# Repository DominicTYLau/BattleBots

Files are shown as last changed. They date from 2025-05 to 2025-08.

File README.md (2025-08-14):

# BattleBots

**Description:

** This project contains two battle bots that are meant to battle each other. One has a vertical spinner while the other has a horizontal one. The chassis is mostly 3D printed with some electronics for the drive base. Both bots are powered by Raspberry Pi Zero 2 W boards, each running a local server. Users connected to the same Wi-Fi network can control the bots through a web interface using arrow keys for movement and the space bar to activate the weapon.

**Motivation for this project:** I made this project because I’ve watched the larger bots and it was fun to see stuff being destroyed.

ROBOT 1: Full CAD https://a360.co/3ZUvcW5

ROBOT 2: Full CAD https://a360.co/43yXR5A

## Demo:

https://youtu.be/-OPFYqFXoV8

## Pictures:
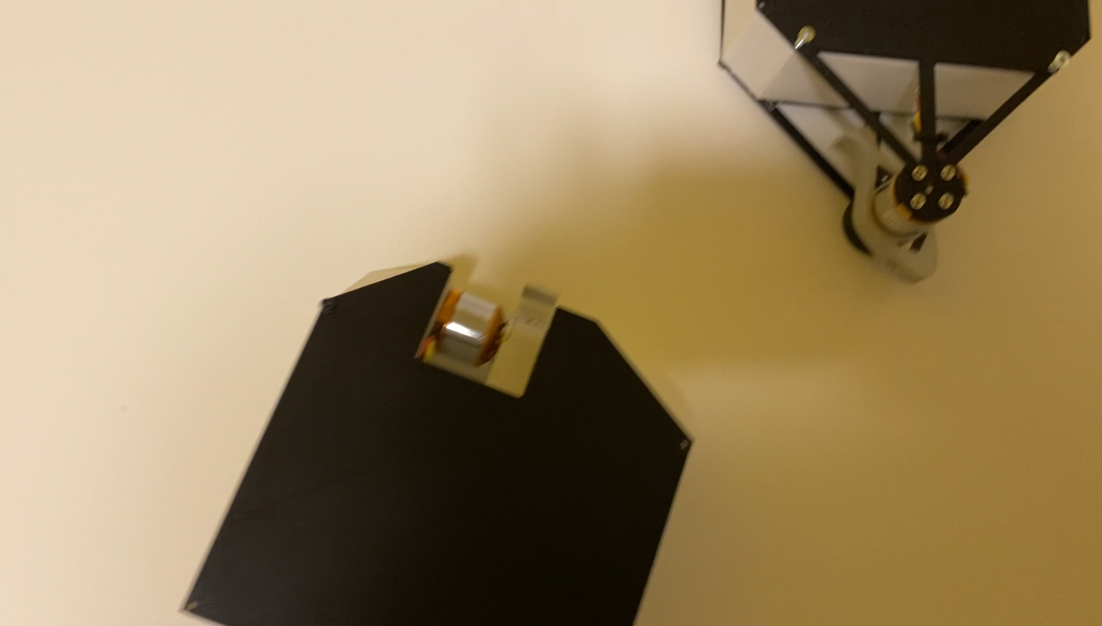
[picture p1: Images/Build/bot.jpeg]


Wiring Diagram:

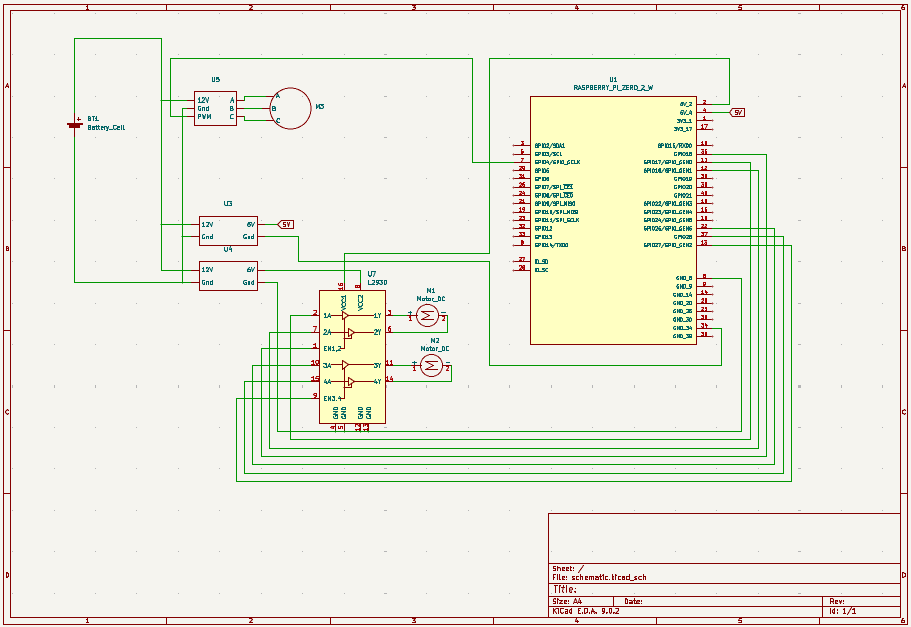
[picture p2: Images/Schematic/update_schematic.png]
High Level Schematic


## BOM:

Purchase Item:

| Item Name | What the Item Is For in Your Project | Item Source | Item Price (USD) | Quantity | Total Price (USD) | URL |
|---|---|---|---|---|---|-----|
| DC 6V Motor with gear | Used for drive motors for the robot | Amazon | 6.71 | 1 | 6.71 | [Link](https://www.aliexpress.com/item/1005005847467025.html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...) |
| CNHL 3S Lipo Battery 2200mAh 30C 11.1V (2 Packs) | Used to power Robots | Amazon | 34.72 | 1 | 34.72 | [Link](https://www.amazon.ca/CNHL-Battery-Airplane-Helicopter-Quadcopte/dp/B0B6N7BTVN/) |
| RC B3 LiPo 2S-3S Battery Charger | Used to charge lipo battery | Amazon | 12.11 | 1 | 12.11 | [Link](https://www.amazon.ca/Battery-Balancer-Charger-7-4-11-1V-Compact/dp/B06XR87987/) |
| 10pcs DC to DC Buck Converter Modules | Step down to different voltages | Amazon | 14.53 | 1 | 14.53 | [Link](https://www.amazon.ca/Podazz-Efficiency-Regulator-stabilization-Converter/dp/B0CTH5Q2KT/) |
| Wago Connectors | Connect wires, reduce mess | Amazon | 7.59 | 1 | 7.59 | [Link](https://www.amazon.ca/WAGO-221-412-Lever-Nuts-2-Conductor-Connectors/dp/B07W4RQ6R6/) |
| Terminal Connectors | Power distributions on protoboard | Aliexpress | 3.56 | 1 | 3.56 | [Link](https://www.aliexpress.com/item/1005006642865467.html) |
| Protoboard (2-8) | Power distributions | Aliexpress | 1.77 | 1 | 1.77 | [Link](https://www.aliexpress.com/item/1005006829112244.html) |
| CNC for weapon | BattleBot Weapon | JLCPCB | 83.50 | 1 | 83.50 | - |
| **Total** | | | | | **164.49** | |

Already Have

| Item | What the Item Is For in Your Project | Quantity |
|---|---|---|
| Pi Zero | Microcontroller | 2 |
| Brushless Motor | Motor | 2 |
| NRF24L01 | Transceiver | 4 |
| ESC | ESC for motor | 2 |
| Arduino Uno | Microcontroller | 2 |
| Joystick | Joystick | 4 |
| Push Button | Button | 2 |
| Bearings | For weapon system | 2 |

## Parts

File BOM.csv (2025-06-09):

Item name | What the item is for in your project | Item source | Item price (include shipping + taxes) | Quantity | Total price (USD) | URL
DC 6V Motor with gear | Used for drive motors for the robot | Amazon | 6.71 USD | 1 | 6.71 | https://www.aliexpress.com/item/1005005847467025.html?scm_id=1007.40050.354490.0&scm-url=1007.40050.354490.0
CNHL 3S Lipo Battery 2200mAh 30C 11.1V with XT60 Plug for RC Car Airplane Helicopter Quadcopte Drone,Racing Hobby(2 Packs) | Used to power Robots | Amazon | 34.72 USD | 1 | 34.72 | https://www.amazon.ca/CNHL-Battery-Airplane-Helicopter-Quadcopte/dp/B0B6N7BTVN?rnid=11192166011
RC B3 LiPo 2S-3S Battery Balancer Charger 7.4v-11.1V RC Pro Compact Charger B3AC | Used to charge lipo battery | Amazon | 12.11 USD | 1 | 12.11 | https://www.amazon.ca/Battery-Balancer-Charger-7-4-11-1V-Compact/dp/B06XR87987
10pcs DC to DC High Efficiency Voltage Regulator Step Down Module 2596 Voltage stabilization 24V to 12V 5V 3V Buck Converter | Used to step down to different voltages for each component | Amazon | 14.53 USD | 1 | 14.53 | https://www.amazon.ca/Podazz-Efficiency-Regulator-stabilization-Converter/dp/B0CTH5Q2KT
Wago Connectors | Connect wires together, decrease mess when wiring | Amazon | 7.59 USD | 1 | 7.59 | https://www.amazon.ca/WAGO-221-412-Lever-Nuts-2-Conductor-Connectors/dp/B07W4RQ6R6?rnid=11192166011
Terminal Connectors | Power distributions on protoboard | Aliexpress | 3.56 USD | 1 | 3.56 | https://www.aliexpress.com/item/1005006642865467.html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
Protoboard (2-8) | Power distributions | Aliexpress | 1.77 USD | 1 | 1.77 | https://www.aliexpress.com/item/1005006829112244.html?scm_id=1007.40050.354490.0&scm-url=1007.40050.354490.0
CNC for weapon | BattleBot Weapon | JLCPCB | 83.5 USD | 1 | 83.5
 |  |  |  |  | 164.49
Already Have
Item | What the item is for in your project | Quantity
Pi zero | Microcontroller | 2
Brushless Motor | motor | 2
NRF24L01 | Transceiver | 4
ESC | ESC for motor | 2
Arduino Uno | Microcontroller | 2
Joystick | Joystick | 4
Push Button | Button | 2
Bearings | For weapon system | 2

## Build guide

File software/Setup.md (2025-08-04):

## Prerequisites

- Raspberry Pi (with GPIO support)
- Motors + ESC connected to correct GPIO pins
- Python 3 installed
- Access to the same Wi-Fi network as your control device

## Wiring

Update the GPIO pin numbers in the script if your wiring differs.

## Setup Instructions

### 1. Connect to Raspberry Pi

### 2. Clone this repository (or copy the script)

Go to the repository

### 3. Create a virtual environment

```bash
python3 -m venv venv
source venv/bin/activate
```

### 4. Install dependencies
```bash
pip install gpiozero
```

Note: RPi.GPIO is preinstalled on most Raspberry Pi systems.

### 5. Set your Raspberry Pi’s IP address in the script

```bash
host_name = "IP_ADDRESS"
```
to your Pi’s actual local IP (e.g., "192.168.1.42")

### 6. Run the server

python3 botOne.py

If successful, you should see:

Server Starts - IP_ADDRESS

### 7. Open the controller

On a device connected to the same Wi-Fi network, open a browser and go to:

http://<raspberry-pi-ip>:8000

Controls
	•	↑ / ↓ — Forward / Backward
	•	← / → — Move left / right
	•	Spacebar — Toggle ESC-powered motor (weapon)

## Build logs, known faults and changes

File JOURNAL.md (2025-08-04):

---
title: "Battle Bot"
author: "Dominic Lau"
description: "Two Battle Bots to break each other"
created_at: "2024-06-01"
---

Time Spent: 28.5 hours

# Planning & Designing

---

## May 15, 2025

Highway was announced and it's a great time to make a project that I've always wanted. 2 BattleBots to break each other. The big challenge for this project is to make sure they both work in order to do damage.

I started by watching a lot of BattleBots and trying to find different designs from different weight classes. I then drew a couple designs that I liked.

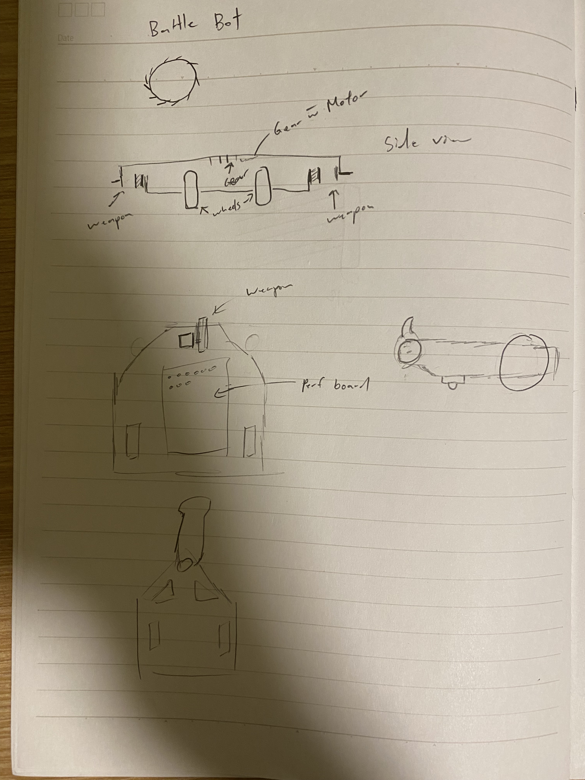
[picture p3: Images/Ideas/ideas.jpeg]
ideas


Time Spent: Around 1 hour

## May 16, 2025

Now that I had the idea, I wanted to determine how to build it. I first decided what main components I need to make this idea possible. Each robot needs to be controlled (user feedback), drive, and spin up a weapon system. Once I had an idea of the requirements, I made some high level diagrams to figure how to wire the robots. I also made a power distrubution diagram. This part is quite expensive because different components requires different voltages. In my past experiences, power is the hardest for the projects. This time, I want to wire as neatly as possible. I then broke the BOM into two main sections. Electoronics and Mechanical. After I listed everything I classified them into things I already have and things that I needed to buy. Afterwards, I went on amazon (cheapest and fastest place to get electronics for me) to find the items that I'm missing. I spent a lot of time trying to optimize the budget and keep the cost low. The current buy items are in [BOM.csv](./BOM.csv). 

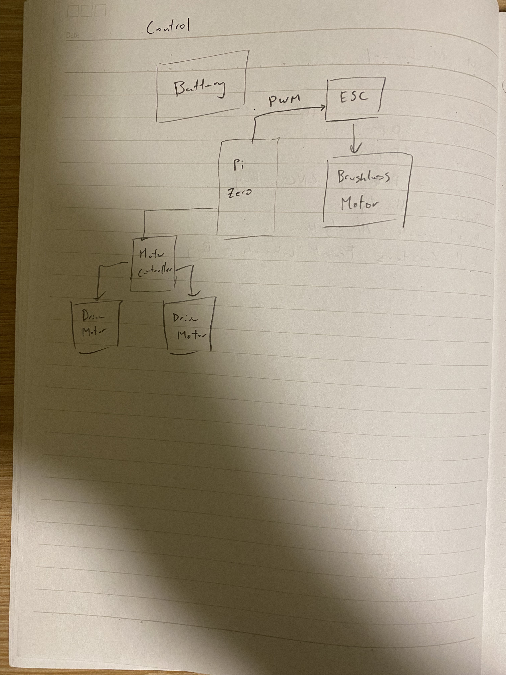
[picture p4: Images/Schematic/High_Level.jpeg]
High Level Schematic

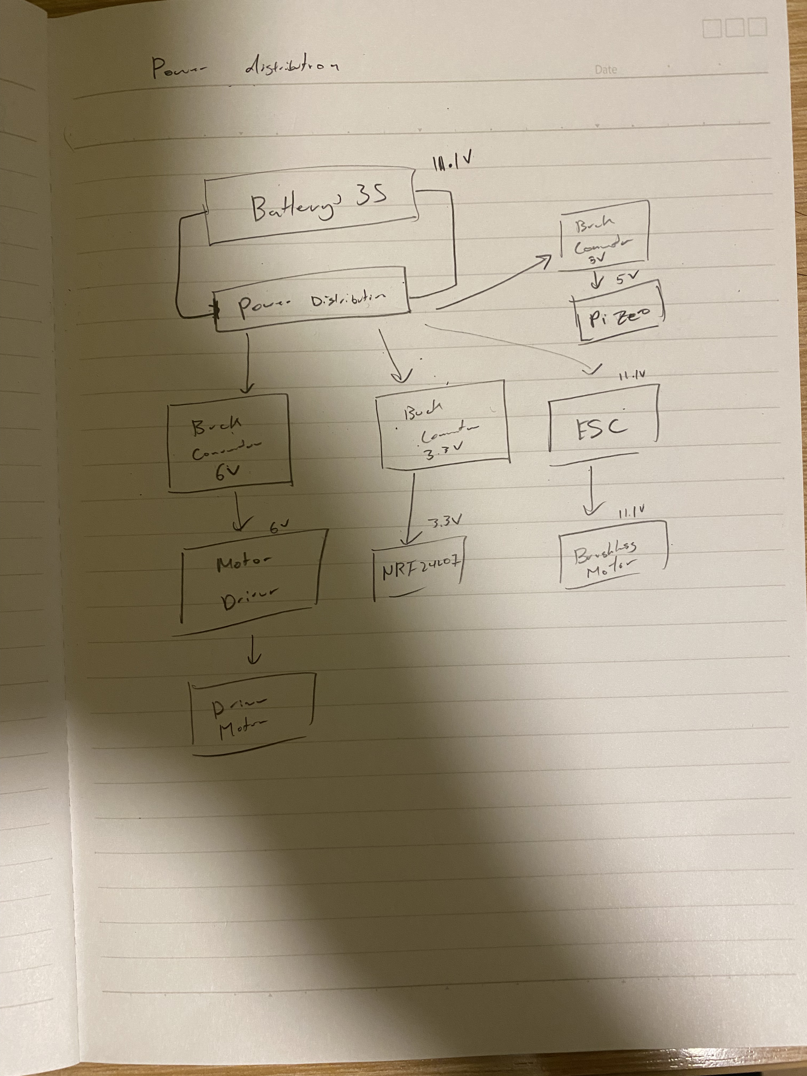
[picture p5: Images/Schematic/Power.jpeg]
Power Distribution

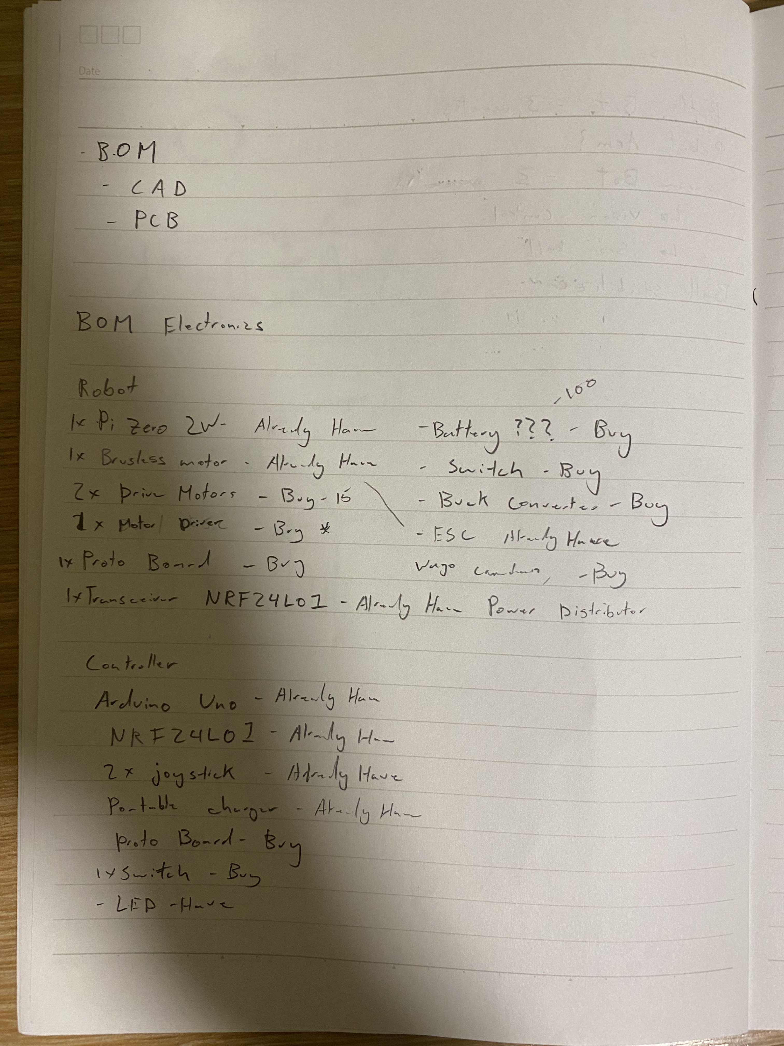
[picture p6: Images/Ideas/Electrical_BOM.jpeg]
Electrical BOM

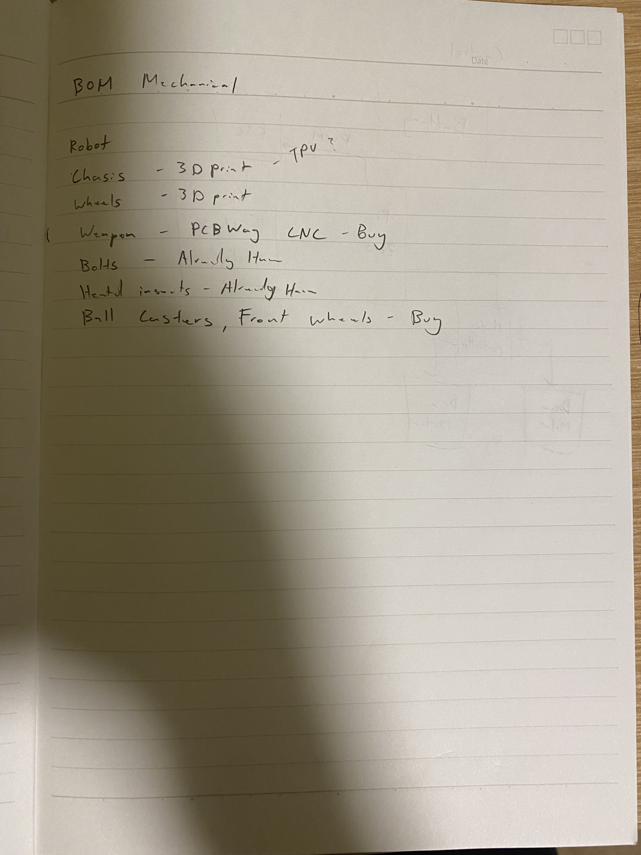
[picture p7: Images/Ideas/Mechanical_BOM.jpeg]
Mechanical BOM


Time Spent: 3 hours

## May 17, 2025

Today I spent a lot of time cading out the design. I first started by 150 mm x 150 mm square and placed each component inside where I think would best fit. After I was happy with it I moved on making it 3D. I worked on the front where I had to learn how to create planes at angles to create the angled ramps at the front of the robot. I also caded up the weapon assembly for bot 1. For bot 2, I took similar layout from bot 1 and changed where the weapon is and its support.

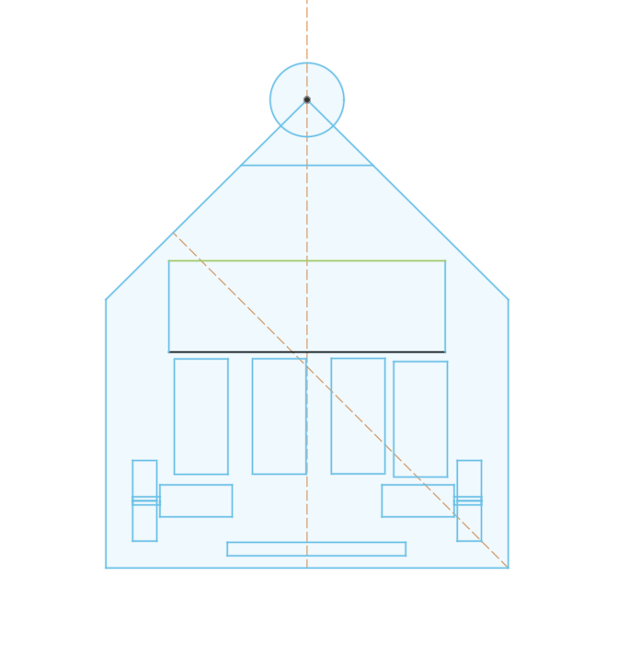
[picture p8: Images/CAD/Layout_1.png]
layout 1

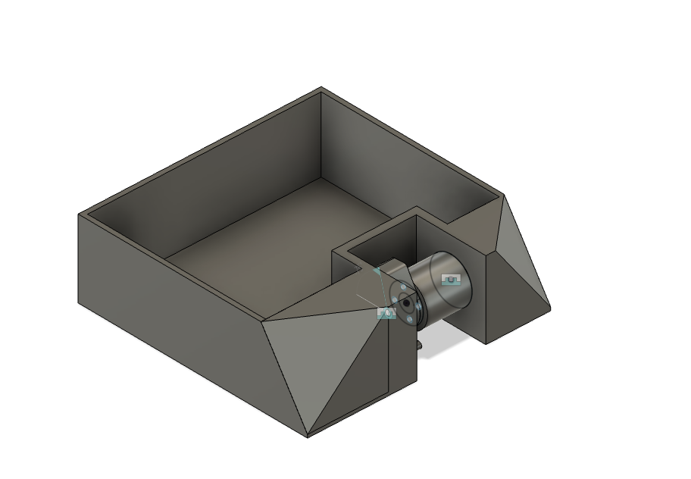
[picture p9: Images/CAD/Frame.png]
frame

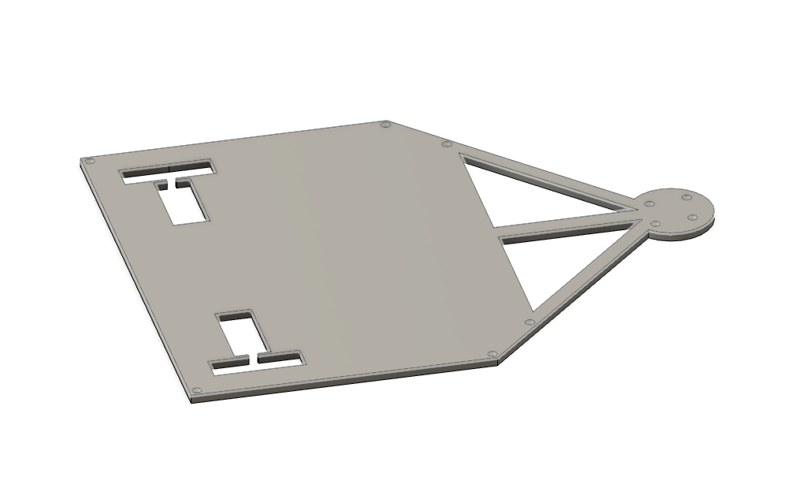
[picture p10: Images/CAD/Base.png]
base

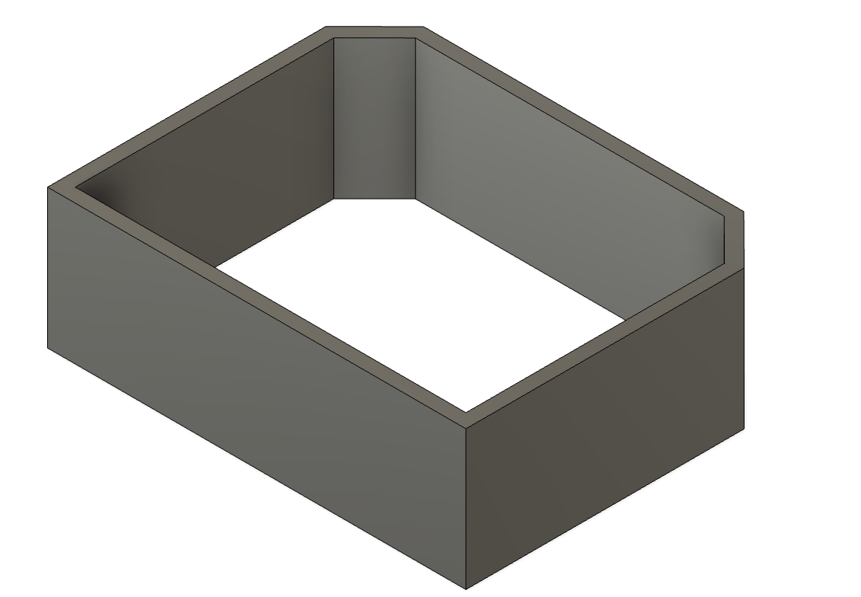
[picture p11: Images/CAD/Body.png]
body


Time Spent: 2.5 hours

## May 18, 2025

Once I had both chasis done, I decided to try and fit the components in the chassis. I followed my original layout and it worked pretty well. I also made the weapon assembly for bot 2. Most of the cad is done for bot 2. For bot 1 I added all the components but as I was adding a top I realized I made the chassis too short so I increased. However, this changed all my other values and so it looks like a mess right now. I’ll fix that for tomorrow and create a schematic.

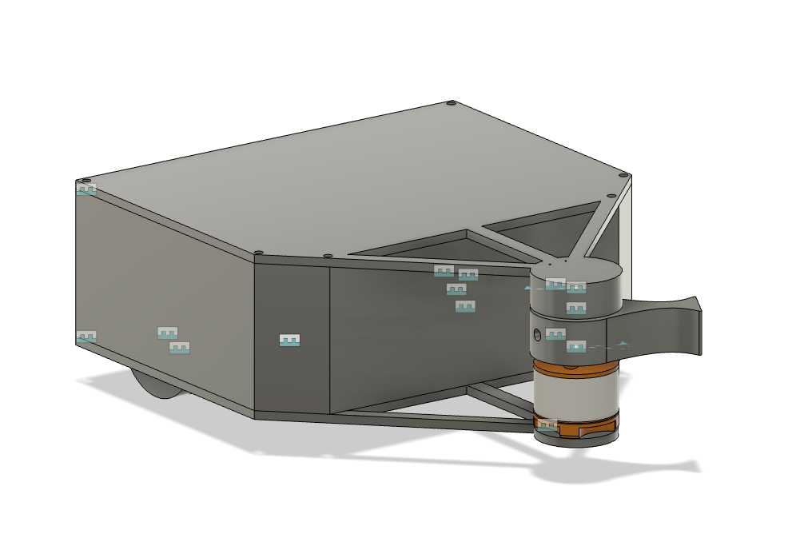
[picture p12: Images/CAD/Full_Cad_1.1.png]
cad 1.1

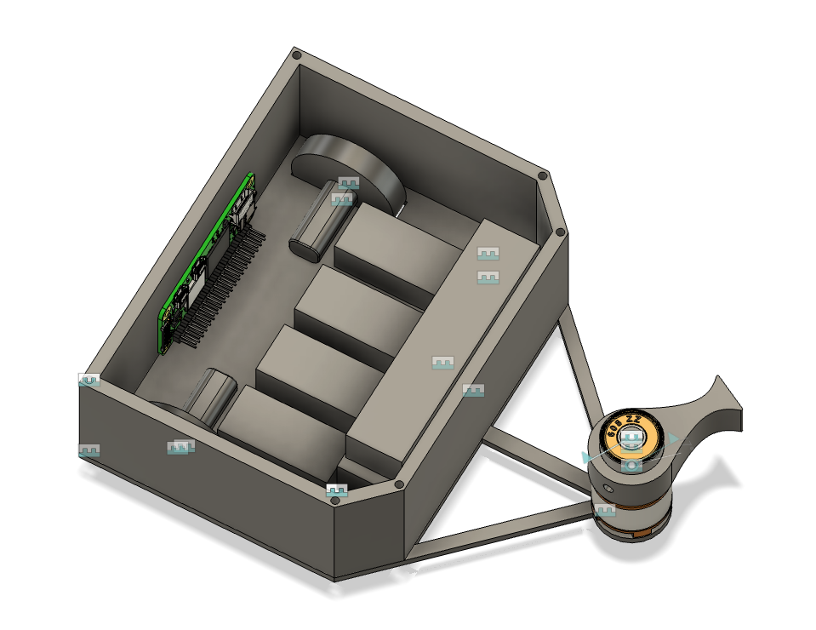
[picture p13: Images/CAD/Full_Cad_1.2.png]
cad 1.2

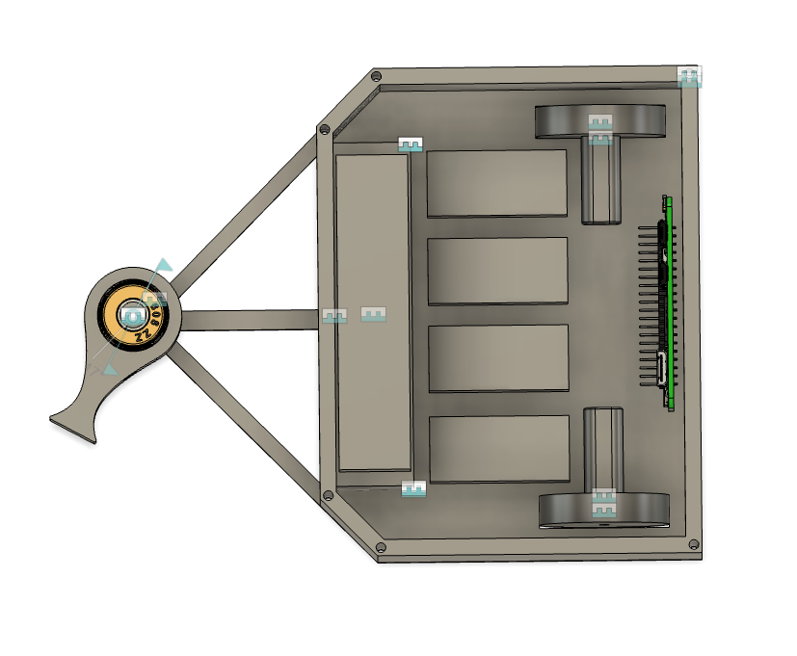
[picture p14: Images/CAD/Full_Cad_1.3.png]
cad 1.3

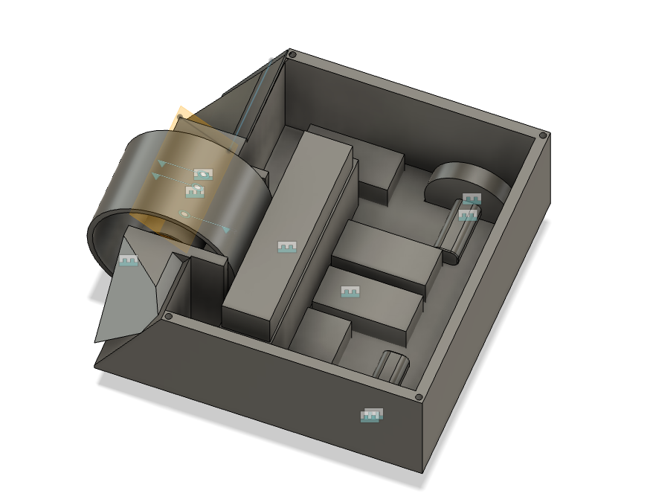
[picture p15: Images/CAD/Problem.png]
problme


Time Spent: 3 hours

## May 19, 2025

I fixed up the bot 1 which took a while. I had to go back in the timeline and change a lot of parameters and remake the sketches.

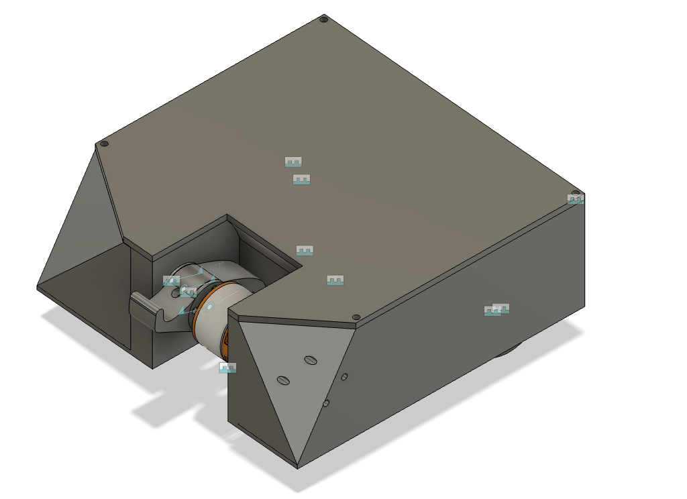
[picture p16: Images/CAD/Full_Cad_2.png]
Robot 2


Time Spent: 1 hour

## May 20, 2025

I made the schematic for the robot. I had to search a lot of the pinouts and I also finally figured out the motor controller for the drive wheels. I’ll be using the L293D which I already have. I also wrote some of the firmware for the pi and the arduino controller. I learned that it’s not a good idea to have the cg of the weapon away from the point of rotation. As a results, I remade it to change the cg position.

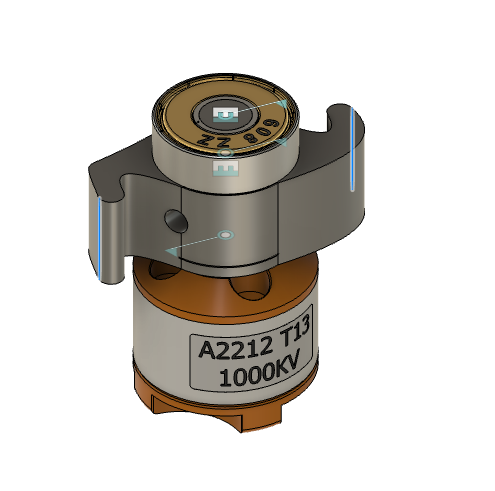
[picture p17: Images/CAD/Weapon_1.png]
weapon

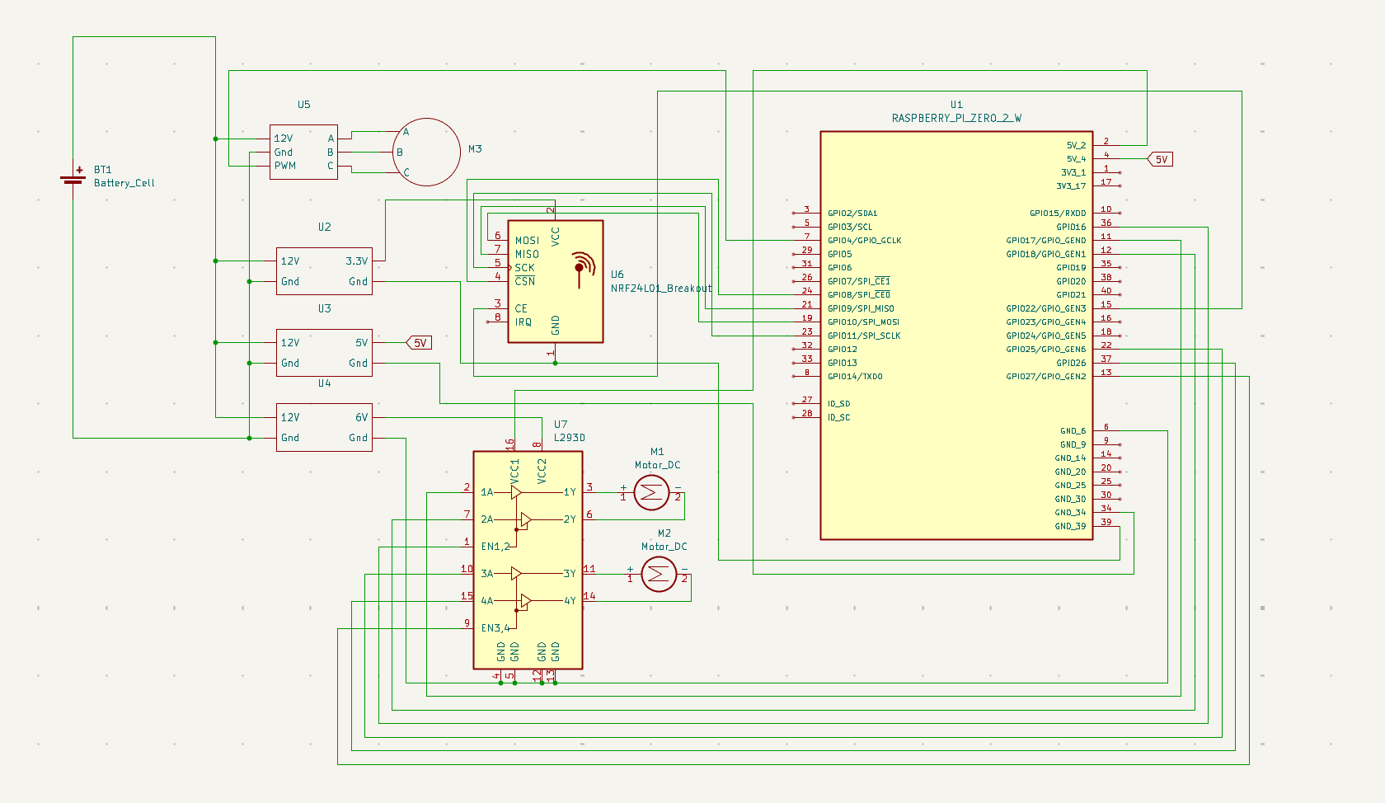
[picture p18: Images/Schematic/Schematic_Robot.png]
Robot Schematic


Time Spent: 1.5 hour

## May 22, 2025

I made sure that my cad was correct with the right dimensions. I added some threads to the weapon system. I contacted places to get quotes for the cnc parts. I also got the general code done. I used previous code from before which had the transceiver.

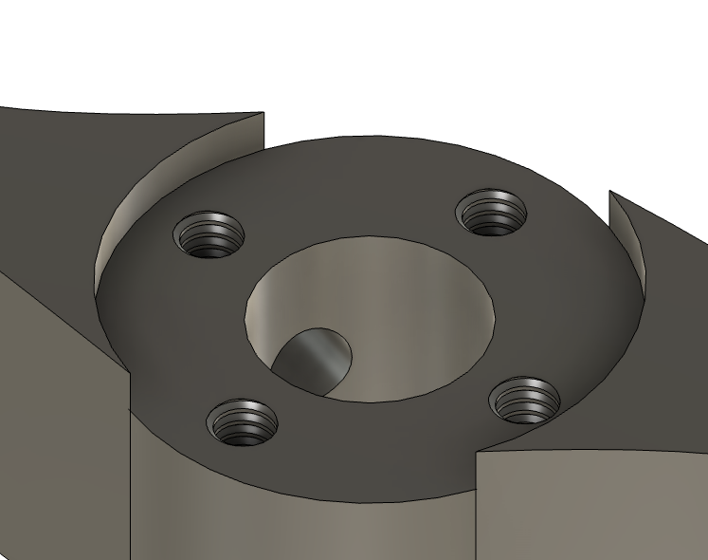
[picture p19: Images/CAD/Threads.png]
Threads


Time Spent: 1.5 hour 

## Jun 8, 2025

I got past the obstacle which was trying to lower the price. I removed some unneecessary parts. I'm still over, but I will pay it out of pocket. I also worked on schematic for the controller and that should be it.

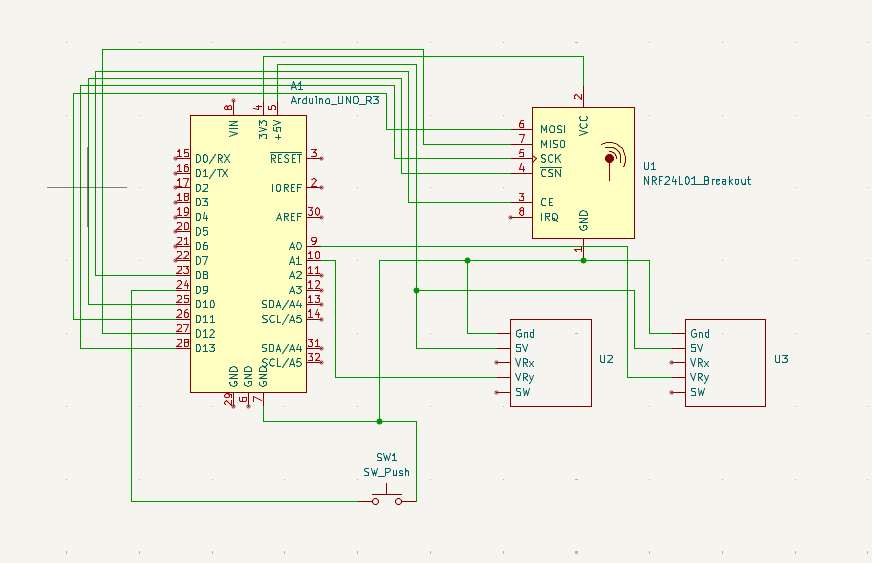
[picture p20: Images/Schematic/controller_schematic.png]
controller_schematic


Time Spent: 0.5 hour

# THE BUILD

---

## Jul 20, 2025

Received all the parts and started 3D printing the components. I began printing the body out of TPU. While that was printing, I soldered wires to the motors and attached the motor controllers to a protoboard with headers for easier connections.

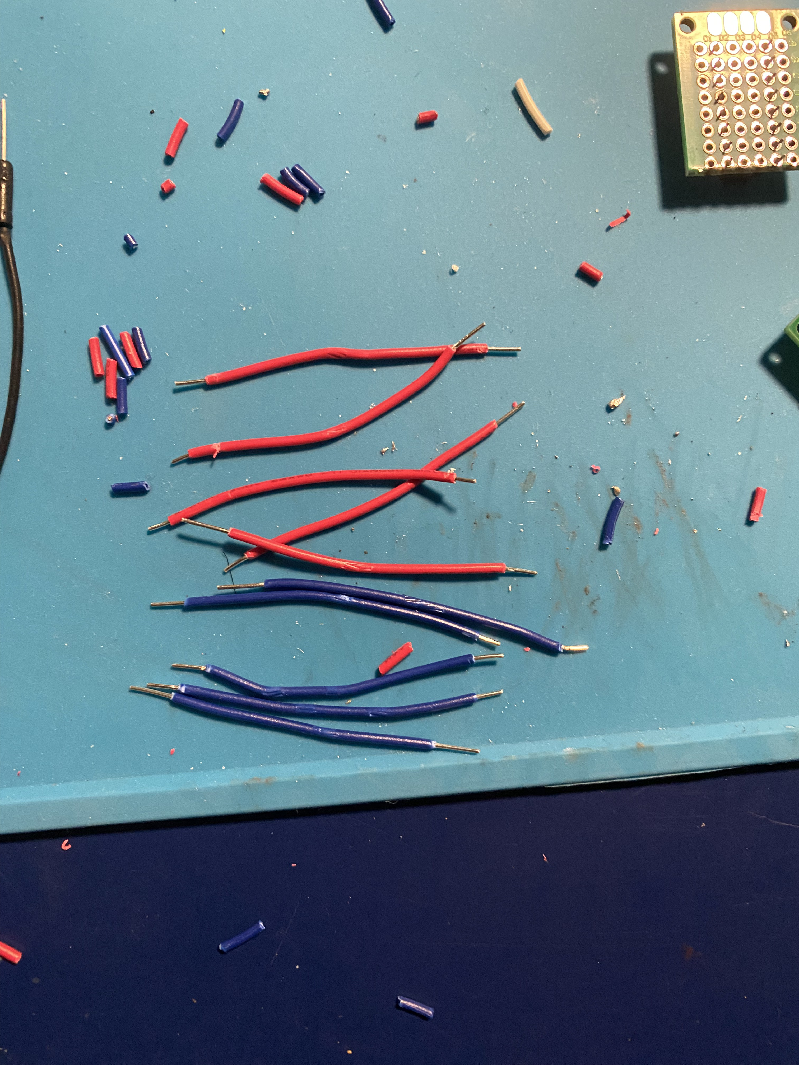
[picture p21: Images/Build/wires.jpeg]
wires

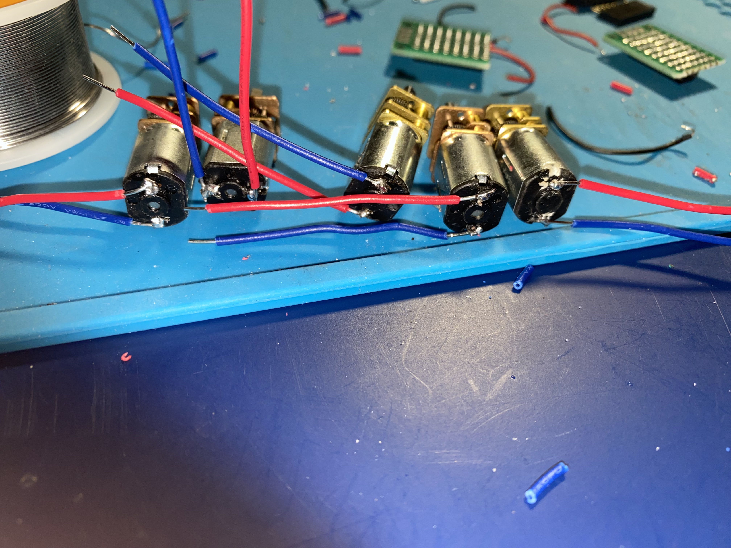
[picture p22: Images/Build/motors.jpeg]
motors

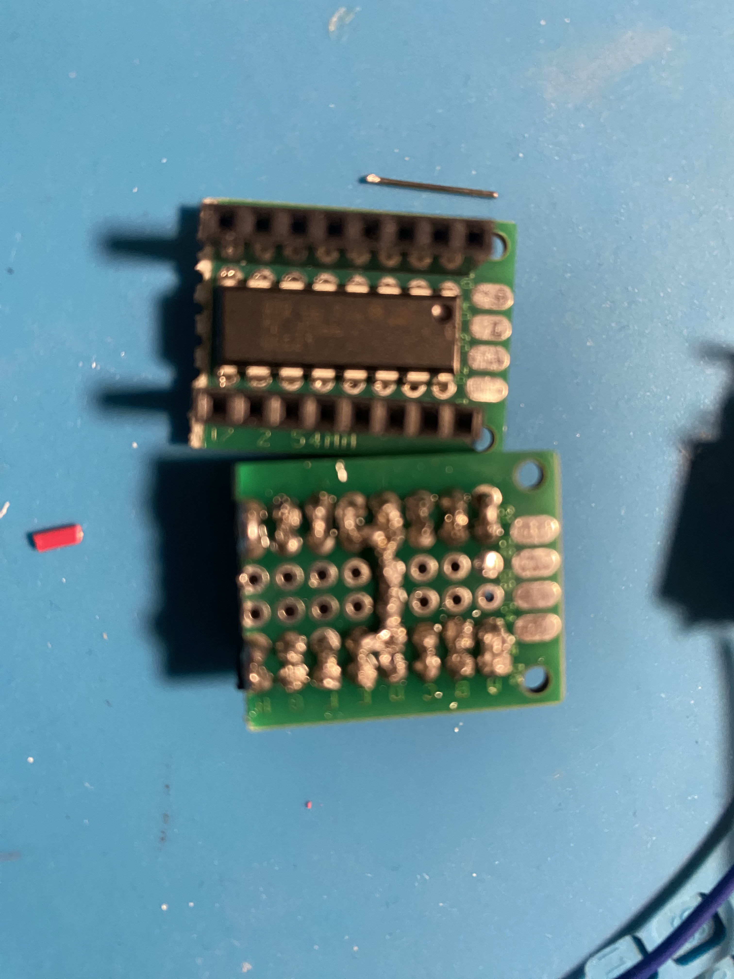
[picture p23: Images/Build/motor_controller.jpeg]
motor_controller


Time Spent: 1.5 hours

## Jul 21, 2025

I soldered more wires to the voltage converters and connected the power distribution protoboard with terminal blocks. I also adjusted the voltage outputs of each converter using a multimeter. I continued printing more parts.

Time Spent: 1.5 hour

## July 22, 2025

I connected the whole circuit and attempted to get things moving. I used SSH to access the Raspberry Pi and was able to write a quick test script to run the motors, including the brushless motor. Setting up the Raspberry Pi took a while. I used SSH along with VSCode’s SSH extension.

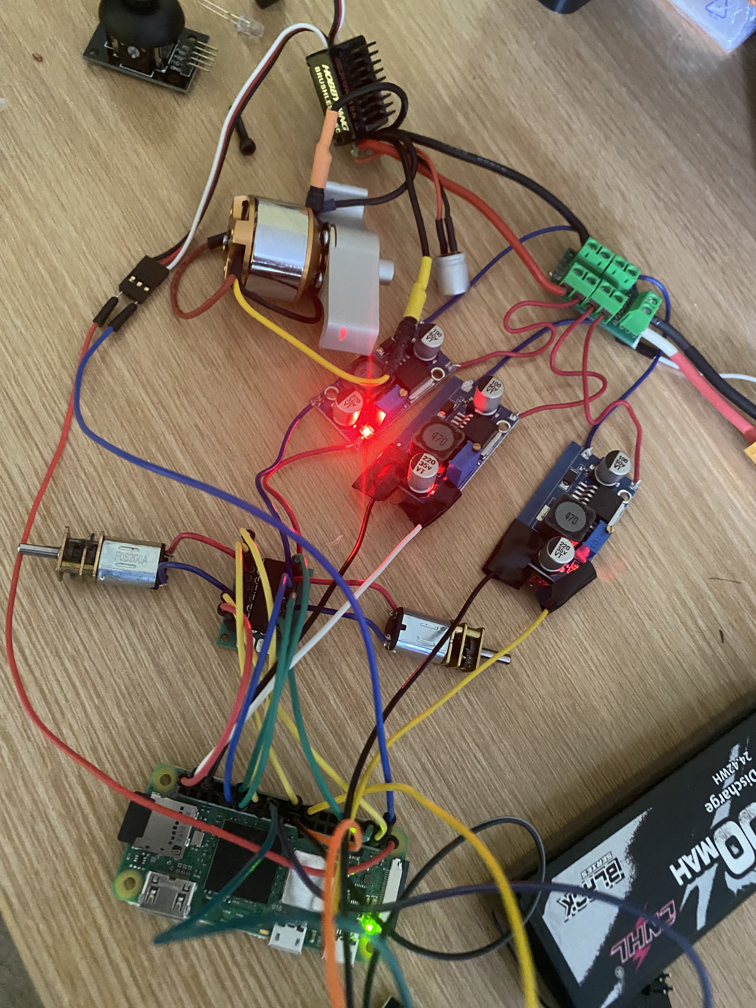
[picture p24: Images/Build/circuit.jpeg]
circuit


Time Spent: 2 hours

## July 23, 2025

I tried to make the same circuit for the other bot and setup the pi but this time the brushless motor would not turn. It would only beep faster. I then tried the motor which beeped the same. I then swapped the Electronic Speed Controller and then it spun. The previous ESC did not work so I had to buy a new one. I also finished printing all the 3D parts.

Time Spent: 2 hours

## July 26, 2025

I had to wait for the new ESC to come but when it came, the ESC was a bit different. The startup was worse, so when throttle or signal was sent it wouldn't spin right away. I had to calibrate and test it multiple times. Once I got that working, I made sure the rest of the motors worked.

Time Spent: 2 hours

## July 27, 2025

I tried hot gluing the dc motors to the chasis but it wasn't sticking. I tried sanding but nothing worked. In the end, I used super glue which worked really well. I also assembled the weapon system which looked terrifying. Once it was done, I squeezed everything into the chassis. I was worried about the wires getting caught on the wheel, but that wasn't a problem when testing. I also used hot glue to make sure that the wires would not be loose. It works pretty well.

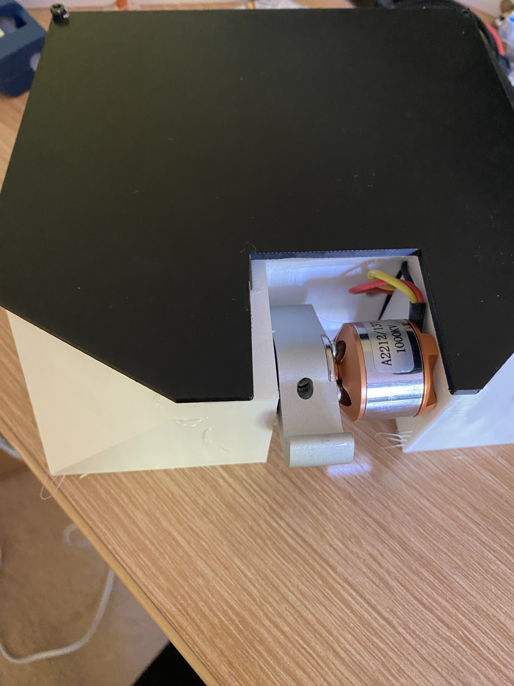
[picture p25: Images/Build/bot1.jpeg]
bot1

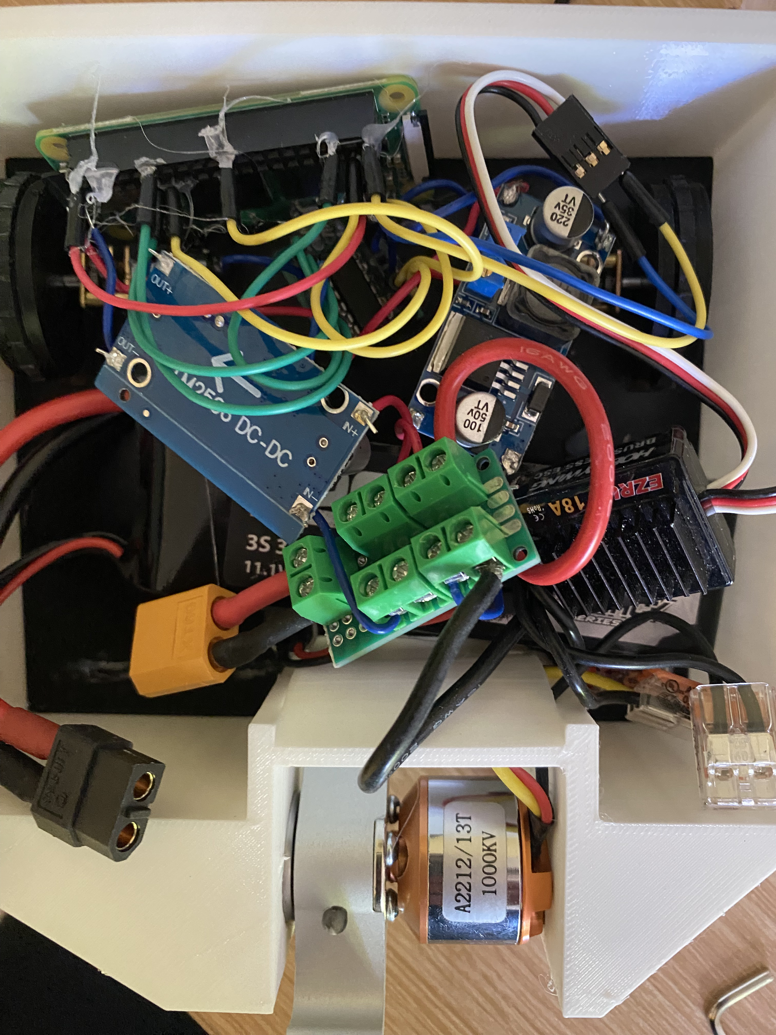
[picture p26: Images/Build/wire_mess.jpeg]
wire_mess


Time Spent: 1.5 hours

## July 28, 2025

I did the same thing to the other bot but ran into an issue. My cad was wrong for the cnc part and I wasn't able to reach the bolt to tighten it to the motor. I had to use a drill and drill to the side. It took a really long time. But in the end, it worked. I got it all built and tested and the bots are terrifying even though they are only running at half speed.

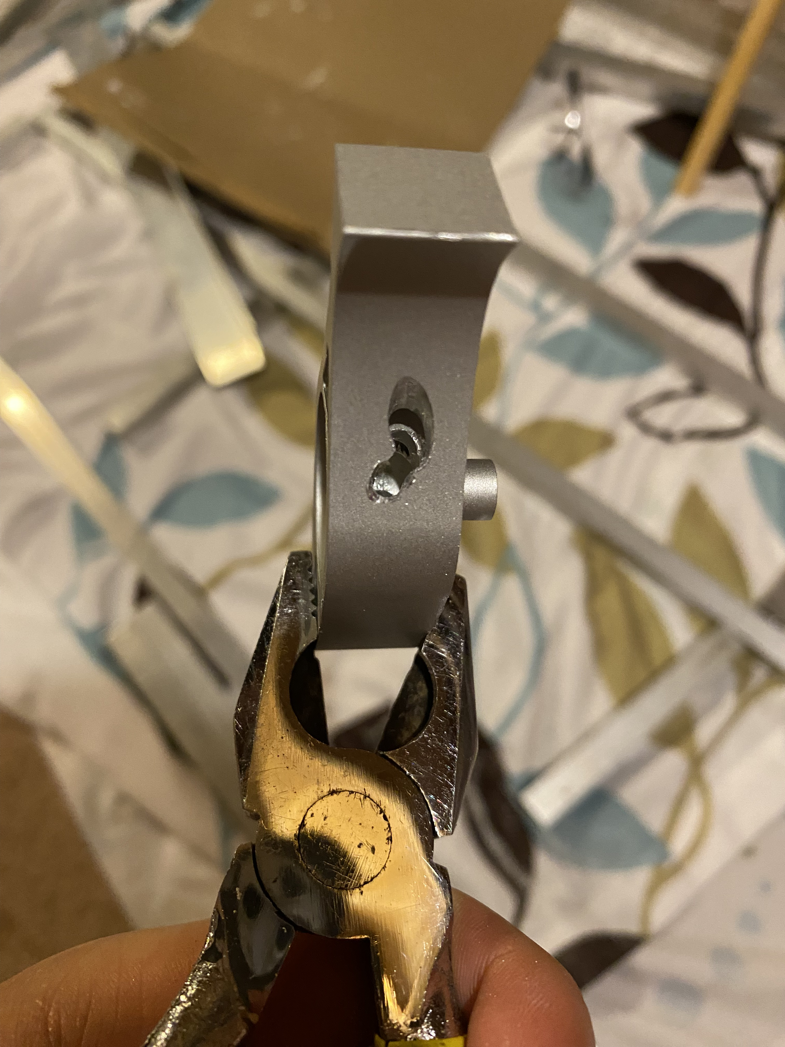
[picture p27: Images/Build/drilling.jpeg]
drilling

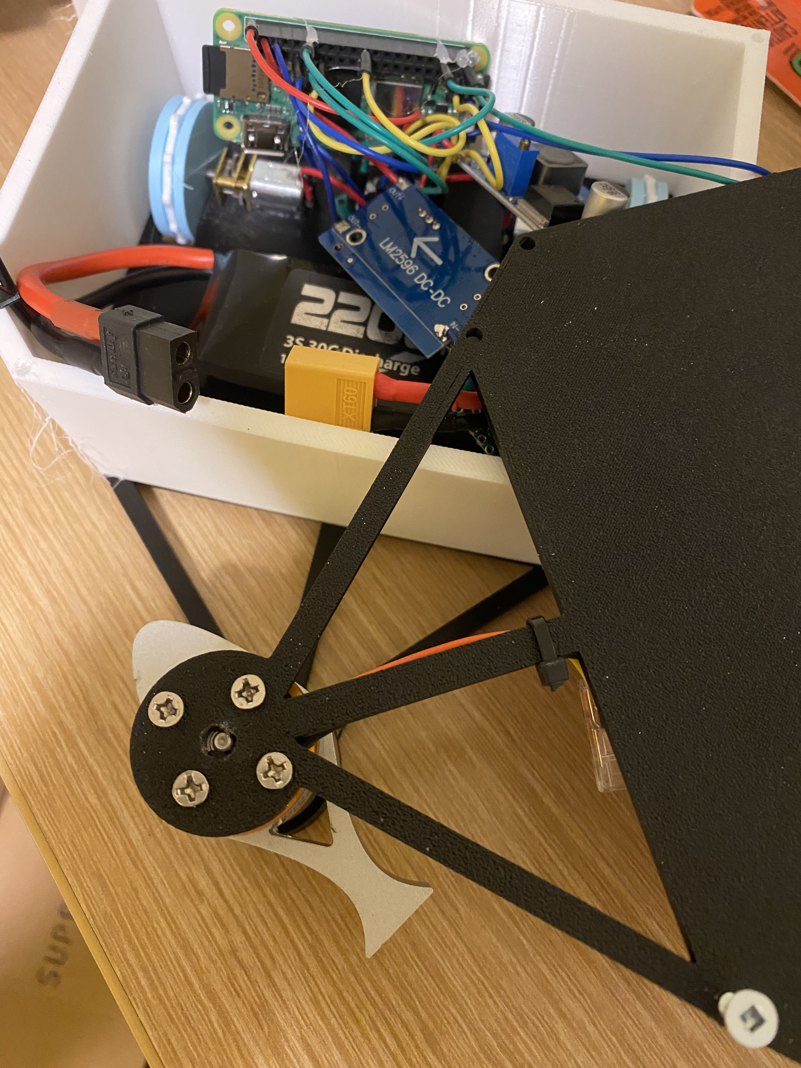
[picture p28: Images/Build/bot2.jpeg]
bot2


Time Spent: 4 hours

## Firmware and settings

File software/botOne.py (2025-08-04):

#!/usr/bin/env python3

import RPi.GPIO as GPIO
from http.server import BaseHTTPRequestHandler, HTTPServer
from gpiozero import Servo
import json
import time

# --- Configuration ---
host_name = "IP_ADDRESS"  # Replace with your Raspberry Pi's IP address
host_port = 8000
esc_pin = 21  # ESC pin

# Motor pin definitions
MOTOR1_IN1 = 25
MOTOR1_IN2 = 26
MOTOR1_EN = 27

MOTOR2_IN3 = 17
MOTOR2_IN4 = 18
MOTOR2_EN = 16

# --- GPIO Setup ---
GPIO.setmode(GPIO.BCM)
GPIO.setwarnings(False)

GPIO.setup(MOTOR1_IN1, GPIO.OUT)
GPIO.setup(MOTOR1_IN2, GPIO.OUT)
GPIO.setup(MOTOR1_EN, GPIO.OUT)

GPIO.setup(MOTOR2_IN3, GPIO.OUT)
GPIO.setup(MOTOR2_IN4, GPIO.OUT)
GPIO.setup(MOTOR2_EN, GPIO.OUT)

# --- PWM Setup ---
motor1_pwm = GPIO.PWM(MOTOR1_EN, 1000)
motor2_pwm = GPIO.PWM(MOTOR2_EN, 1000)

motor1_pwm.start(0)
motor2_pwm.start(0)

# --- ESC Setup using gpiozero ---
ESC_MIN_PULSE = 0.000
ESC_MAX_PULSE = 1.5 / 1000 
esc_servo = Servo(esc_pin, min_pulse_width=ESC_MIN_PULSE, max_pulse_width=ESC_MAX_PULSE)

# --- Motor Control ---
def set_motor(left_speed, right_speed):
    left_speed = max(-100, min(left_speed, 100))
    right_speed = max(-100, min(right_speed, 100))

    # Left motor
    GPIO.output(MOTOR1_IN1, left_speed > 0)
    GPIO.output(MOTOR1_IN2, left_speed < 0)

    # Right motor
    GPIO.output(MOTOR2_IN3, right_speed > 0)
    GPIO.output(MOTOR2_IN4, right_speed < 0)

    motor1_pwm.ChangeDutyCycle(abs(left_speed))
    motor2_pwm.ChangeDutyCycle(abs(right_speed))

    print(f"Set motors → Left: {left_speed}%, Right: {right_speed}%")


def set_esc(active):
    """Spin ESC motor if active=1, else stop."""
    if active:
        esc_servo.value = 1 
        print("ESC: Spinning")
    else:
        esc_servo.value = -1
        print("ESC: Stopped")


# --- HTTP Server ---
class MyServer(BaseHTTPRequestHandler):
    def do_HEAD(self):
        self.send_response(200)
        self.send_header('Content-type', 'text/html')
        self.end_headers()

    def do_GET(self):
        html = '''
       <html>
<head>
    <title>Smart Motor Controller</title>
    <style>
        body {
            font-family: Arial, sans-serif;
            text-align: center;
            margin-top: 50px;
            background-color: #f9f9f9;
        }
        h1 {
            color: #333;
        }
        #status {
            font-size: 20px;
            margin-top: 20px;
            color: #444;
        }
        .instructions {
            margin-top: 30px;
            color: #666;
        }
    </style>
</head>
<body>
    <h1>Use Arrow Keys to Drive</h1>
    <div id="status">Waiting for input...</div>
    <div class="instructions">
        Use arrow keys to drive. Hold <b>Space</b> to spin the ESC motor.
    </div>

    <script>
        let keys = {
            ArrowUp: false,
            ArrowDown: false,
            ArrowLeft: false,
            ArrowRight: false,
            Space: false
        };

        let speed = 70;
        let timeout = null;

        function sendCommand() {
            let forward = keys.ArrowUp ? 1 : keys.ArrowDown ? -1 : 0;
            let turn = keys.ArrowRight ? -1 : keys.ArrowLeft ? 1 : 0;
            let esc = keys.Space ? 1 : 0;

            let left = speed * (forward - turn);
            let right = speed * (forward + turn);

            left = Math.max(-100, Math.min(100, left));
            right = Math.max(-100, Math.min(100, right));

            fetch("/", {
                method: "POST",
                headers: { "Content-Type": "application/json" },
                body: JSON.stringify({ left: left, right: right, esc: esc })
            });

            if (forward === 0 && turn === 0 && !esc) {
                document.getElementById("status").innerText = "Motors stopped.";
            } else {
                document.getElementById("status").innerText = 
                    `Left: ${Math.round(left)}%, Right: ${Math.round(right)}%, ESC: ${esc ? "ON" : "OFF"}`;
            }
        }

        function updateLoop() {
            sendCommand();
            timeout = setTimeout(updateLoop, 100);
        }

        document.addEventListener("keydown", function(e) {
            if (e.key === " ") {
                e.preventDefault(); // Prevent page scroll
                keys.Space = true;
                if (!timeout) updateLoop();
                return;
            }

            if (e.key in keys && !keys[e.key]) {
                keys[e.key] = true;
                if (!timeout) updateLoop();
            }
        });

        document.addEventListener("keyup", function(e) {
            if (e.key === " ") {
                keys.Space = false;
            }

            if (e.key in keys) {
                keys[e.key] = false;

                if (!Object.values(keys).some(v => v)) {
                    sendCommand();
                    clearTimeout(timeout);
                    timeout = null;
                }
            }
        });
    </script>
</body>
</html>
        '''
        self.do_HEAD()
        self.wfile.write(html.encode("utf-8"))

    def do_POST(self):
        content_length = int(self.headers['Content-Length'])
        body = self.rfile.read(content_length)
        data = json.loads(body)

        left = int(data.get("left", 0))
        right = int(data.get("right", 0))
        esc = int(data.get("esc", 0))

        set_motor(left, right)
        set_esc(esc)

        self.send_response(200)
        self.end_headers()


# --- Main Program ---
if __name__ == '__main__':
    http_server = HTTPServer((host_name, host_port), MyServer)
    print(f"Server Starts - {host_name}:{host_port}")

    try:
        http_server.serve_forever()
    except KeyboardInterrupt:
        print("Shutting down...")
        set_motor(0, 0)
        set_esc(0)
        motor1_pwm.stop()
        motor2_pwm.stop()
        esc_servo.detach()
        GPIO.cleanup()
        http_server.server_close()

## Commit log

2025-05-18 Add images
    [BOM.csv]
2025-06-09 controller schematic
    [controller.kicad_pcb, controller.kicad_sch]
2025-06-09 add cad
